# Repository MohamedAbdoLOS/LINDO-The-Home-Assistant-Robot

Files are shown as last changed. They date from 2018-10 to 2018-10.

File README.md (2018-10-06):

# "LINDO" The Home Assistant Robot 
This project introduces a home assistant mobile robot designed to be used for indoor navigation. It can be operated either autonomously or controlled by man remotely over the network. Odometry information is used to estimate the robot's position relative to its origin. In order to achieve a robust odometry, the robot uses two sources of odometry, the linear velocities from the encoders and the angular velocity from the IMU. A Kinect mounted on the robot creates a SLAM map with the help of edge detection and computer vision. The robot can navigate autonomously through the predefined map using AMCL. 

An assistant system is integrated on the robot allows it to communicate and socialize with humans, via a Chatbot powered by Artificial Intelligence and Machine Learning, connected to external APIs to bring realtime information. Also the robot can Automate and Secure your home via an IOT system. 

The project uses The Robots Operating System (ROS) which makes its functionality reusable in other projects. Modularity and readable codes are considered in the design and implementation of software nodes. About future work there is a wide field of updates like object detection, On-line Mapping of new Environments and installation of manipulator (i.e. robot arm) for a variet

## Rendered Designs:
#### Inner Frame:
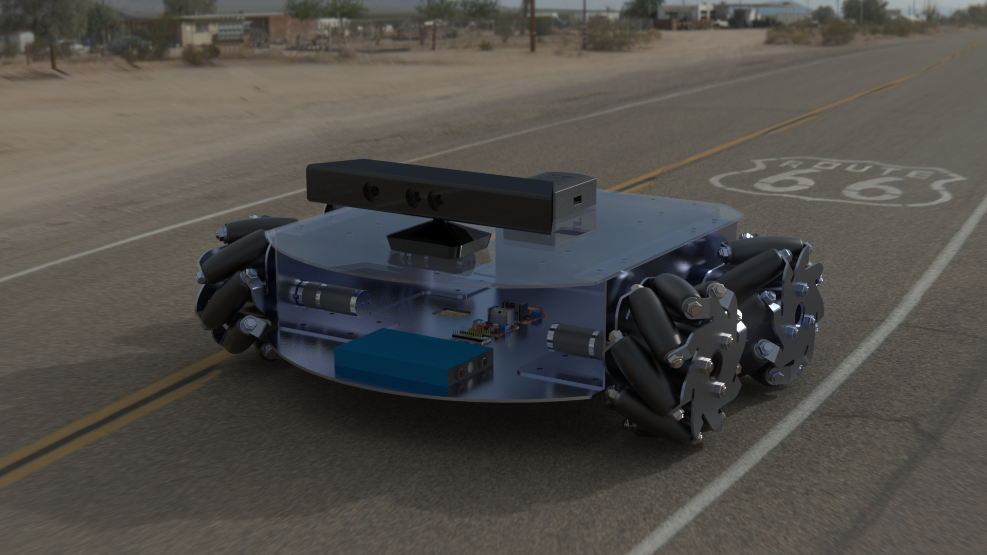
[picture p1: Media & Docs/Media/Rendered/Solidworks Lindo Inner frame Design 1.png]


#### Outer Frame:
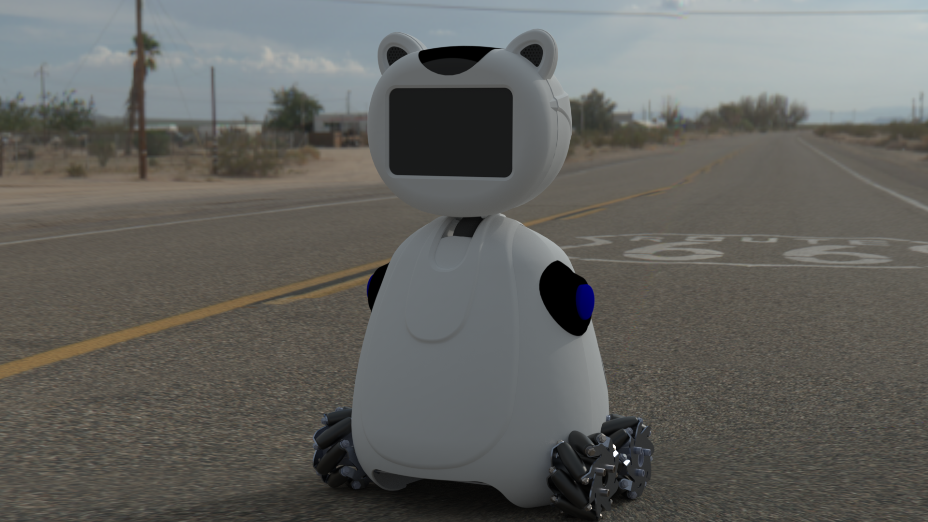
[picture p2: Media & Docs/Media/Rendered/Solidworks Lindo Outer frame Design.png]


## Hardware
- 4 Mecanum Wheels
- 4 Motors 12v 8.8 Kgf.cm
- 4 Encoders 3PPR
- 4 Channels Motor Driver
- Teensy 3.2
- Rasberry PI3
- MPU6050
- Kinect
- 12V Batteries

## Wiring Schematic:
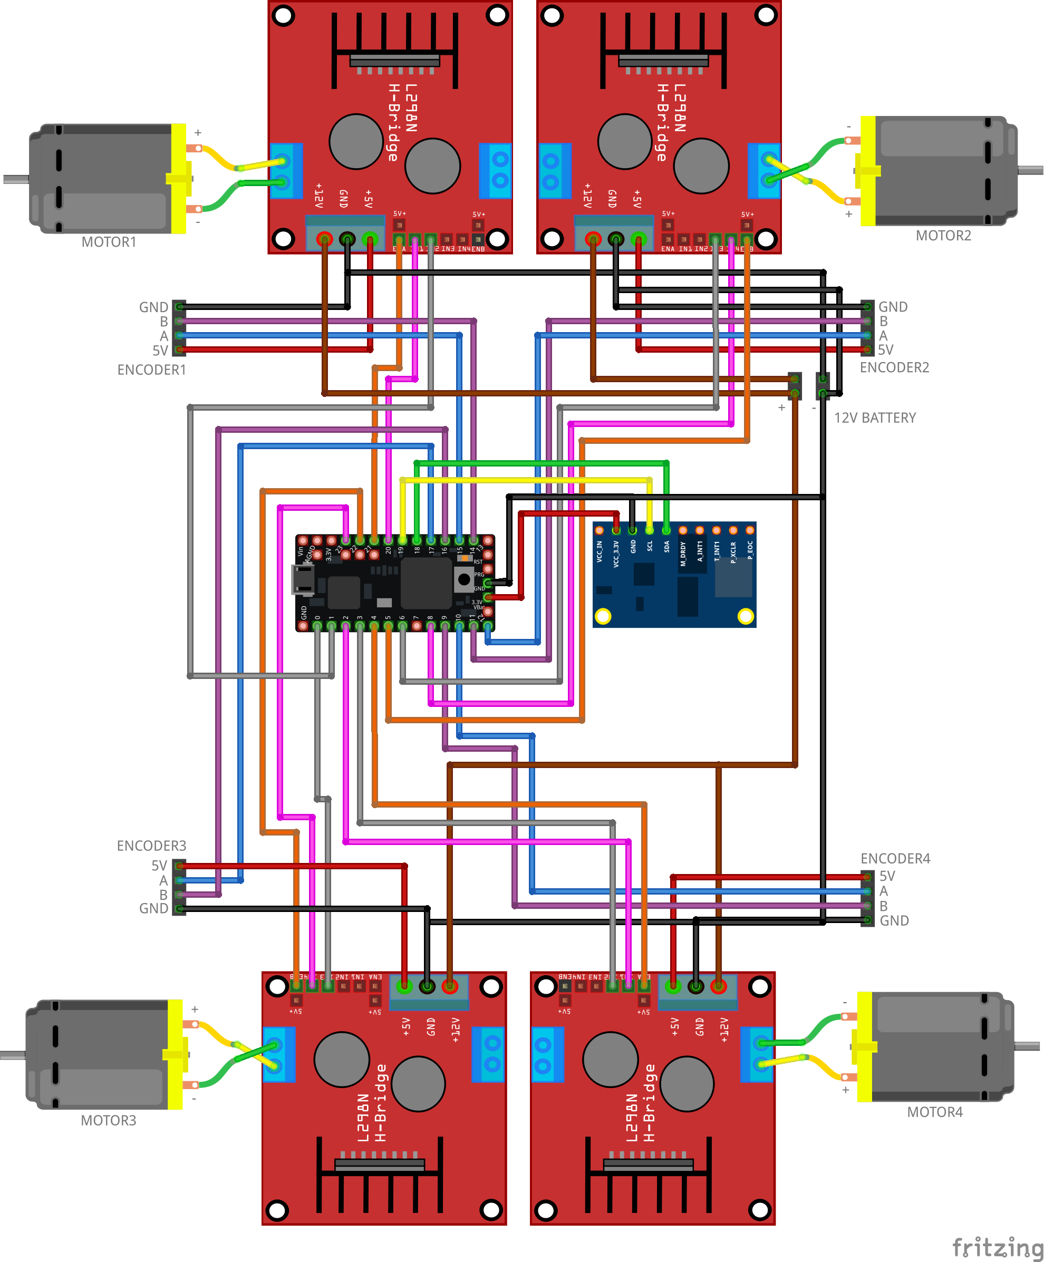
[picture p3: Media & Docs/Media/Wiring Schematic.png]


#### Notes:
- Fritizing doesn't have a 4 Channels Motor Driver yet, so we used an L298 Drivers on the schematic instead.

## Clearifying:
#### Master And Slave:
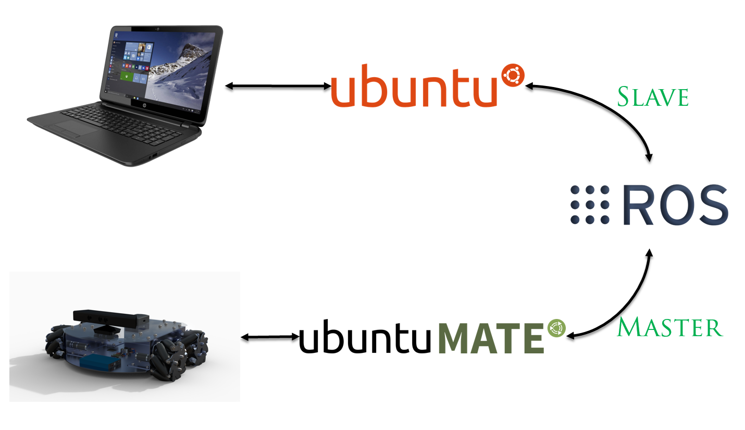
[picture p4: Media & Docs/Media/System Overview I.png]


#### Project Overview:
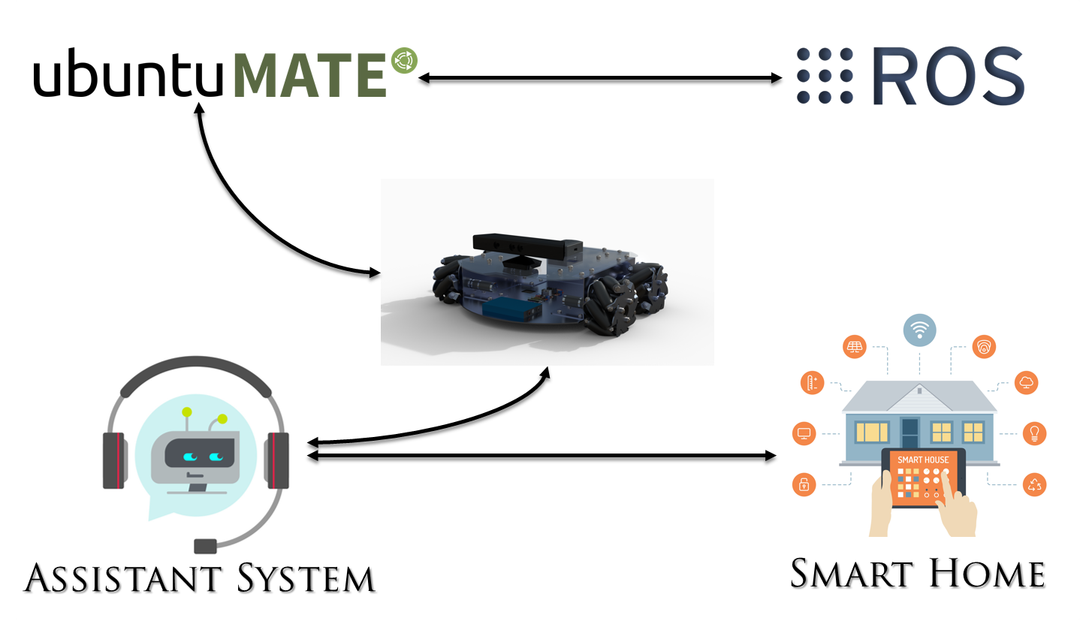
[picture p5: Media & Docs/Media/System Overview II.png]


#### Rasberry PI(ROS) And Teensy:
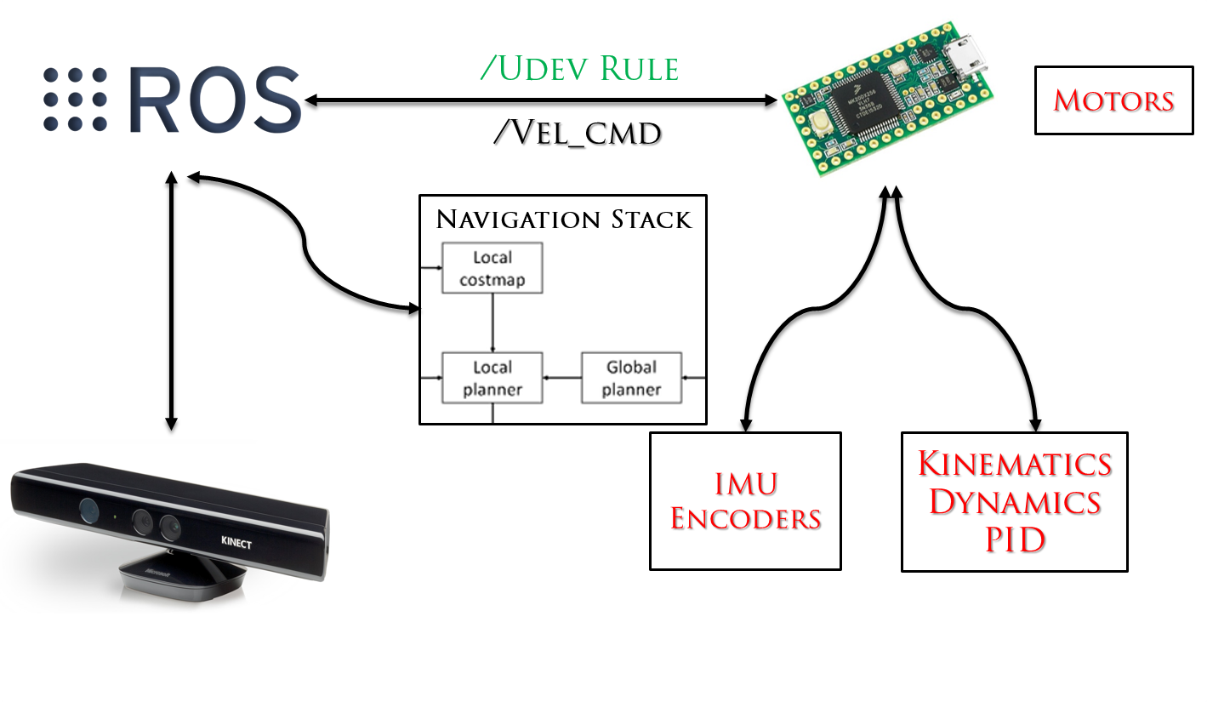
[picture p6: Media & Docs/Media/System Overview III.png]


## Platform:

#### Development Labtop:
- ROS Kinetic (Ubuntu 16.04 Xenial)

#### Rasberry Pi 3:
- ROS Kinetic (Ubuntu Mate 16.04)

## User Manual:
#### Creating a Map:
- On robot’s computer,  Launch base driver:
```
roslaunch lindorobot bringup.launch
```
- On robot’s computer, Launch mapping packages:
```
roslaunch lindorobot slam.launch
```
- On your development computer, run teleop_twist_keyboard:
```
rosrun teleop_twist_keyboard teleop_twist_keyboard.py	
```
- On your development computer, Run rviz:
```
roscd lindo_visualize/rviz
rviz -d slam.rviz
```
- Once you are done mapping save the map by running map_server on the robot's computer:
```
rosrun map_server map_saver -f ~/lindorobot_ws/src/linodorobot/maps/map
```

#### Autonomous Navigation
- Launch base driver, on robot’s computer:
```
roslaunch lindorobot bringup.launch
```
- Launch navigation packages, on robot’s computer:
```
roslaunch lindorobot navigate.launch
```
- On your development computer, run rviz:
```
roscd lindo_visualize/rviz
rviz -d navigate.rviz
```

## Assistant System:
#### Overview Of the Assistant System:
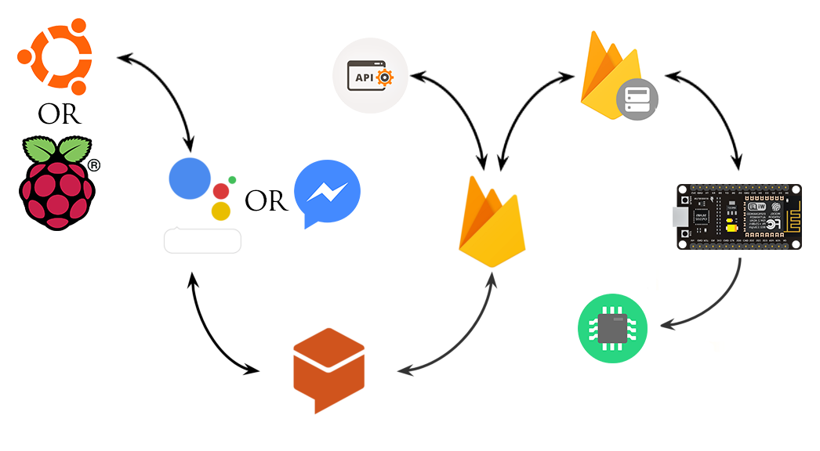
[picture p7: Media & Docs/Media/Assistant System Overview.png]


#### DialogFlow Overview:
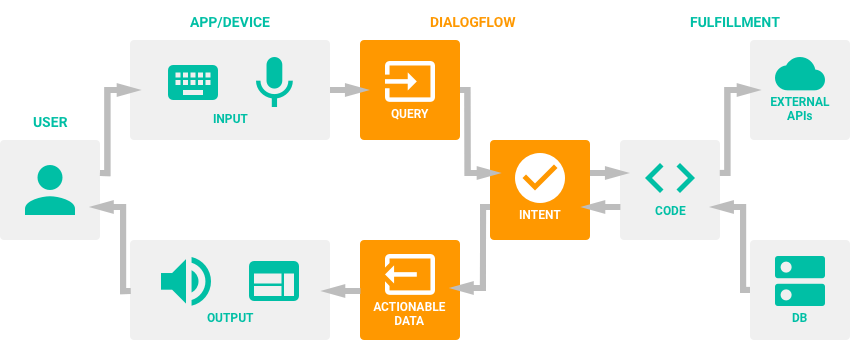
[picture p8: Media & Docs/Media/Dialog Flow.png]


## Videos
- <a href="https://www.youtube.com/watch?v=ZyevQ8gZiK0">"LINDO" - Teleopration Intial Tests[Before PID Tunning]</a>
- <a href="https://www.youtube.com/watch?v=e5AFlajBlEw">"LINDO" - Localization Intial Tests Using IMU and Encoders</a>
- <a href="https://www.youtube.com/watch?v=WcR59p794sQ">"LINDO" - Depth Generation Intial Tests Using Kinect</a>
- <a href="https://www.youtube.com/watch?v=mfHSG0Qb3YM">"LINDO" - Autonomus Driving and Obstacle Avoidance Intial Test </a>
- <a href="https://www.youtube.com/watch?v=wUoYN-ng8Ps">"LINDO" - Assistant System V1 [DialogFlow+Firebase+Database+NodeMCU+APIs]</a>
- <a href="https://www.youtube.com/watch?v=nZiiJRJRGrw">"LINDO" - Assistant System Voice-Ready Intial Test</a>

## TEAM AWAKEN:
#### Members:
- Mohamed Abdo
- Mahmoud Mahmoud
- Islam El-Nagdy
- Ahmed Hamed

#### From:
- MUST University,
- Engineering Faculty,
- Mechatronics Department

#### Contact Us:
- Email: moha_the.best@hotmail.com

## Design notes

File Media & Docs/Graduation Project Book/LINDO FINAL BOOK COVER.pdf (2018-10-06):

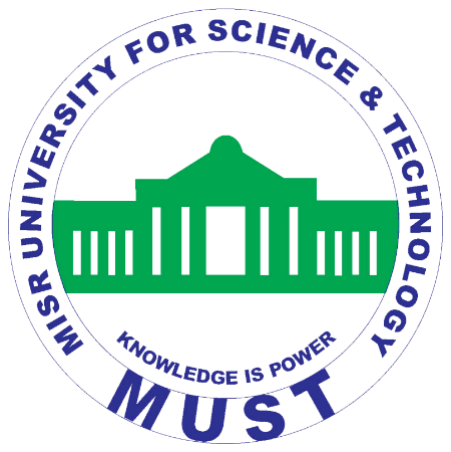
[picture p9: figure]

Misr University for Science & Technology (http://www.must.edu.eg/) Mechatronics Engineering Department Spring/Fall 2017-2018

A B.Sc Senior Project Report Submitted to the Faculty of Engineering at

For the Fulfillment of the Bachelor Degree In

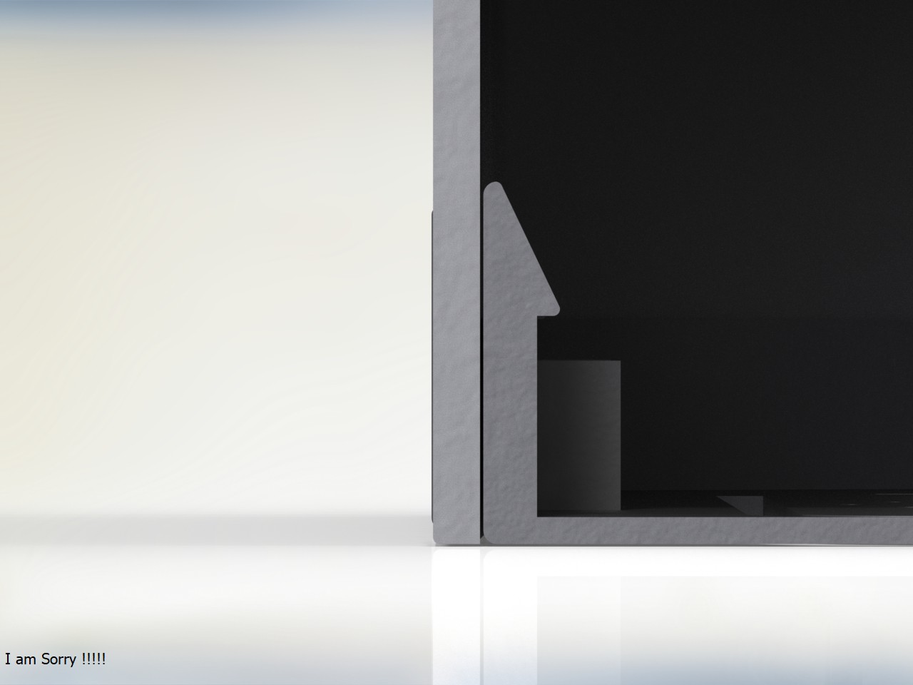
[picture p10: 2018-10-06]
Solidworks Designs/The Robot/Grab Cad folder/Renders/pi section view.JPG

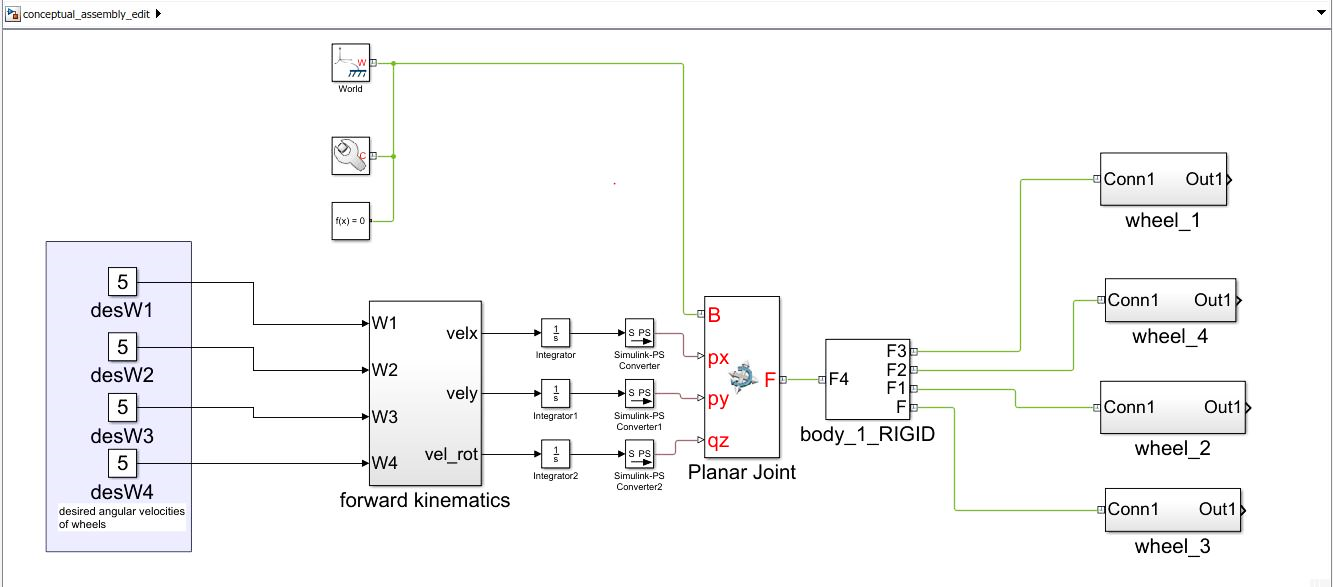
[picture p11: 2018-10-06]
Media & Docs/Media/Kinematics Valdidation I.png

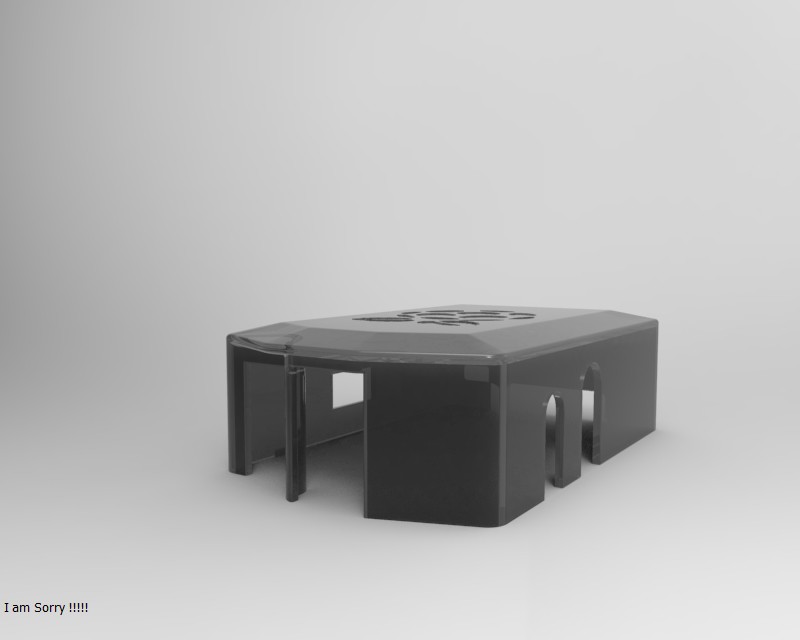
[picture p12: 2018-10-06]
Solidworks Designs/The Robot/Grab Cad folder/Renders/untitled.15.jpg

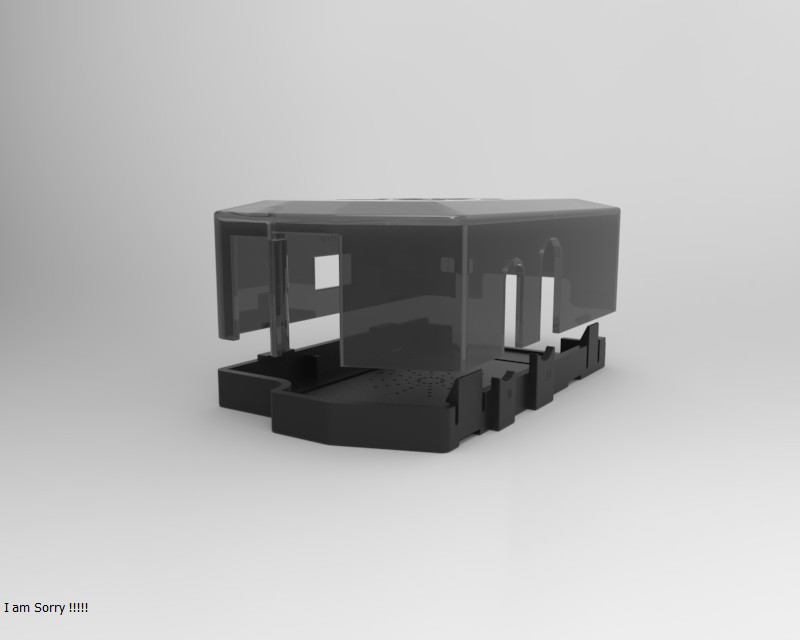
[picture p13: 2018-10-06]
Solidworks Designs/The Robot/Grab Cad folder/Renders/untitled.17.jpg

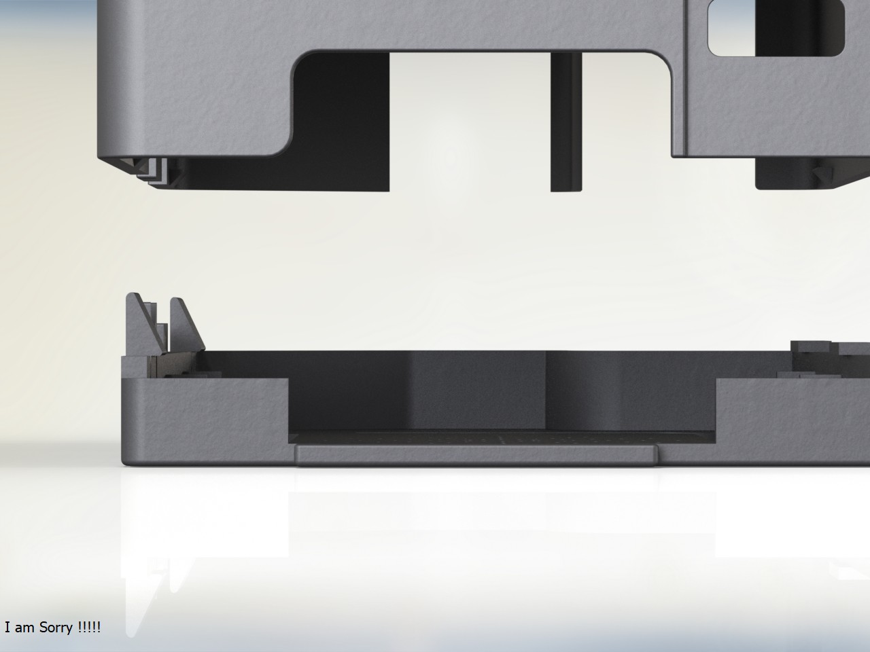
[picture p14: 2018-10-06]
Solidworks Designs/The Robot/Grab Cad folder/Renders/pi8.JPG

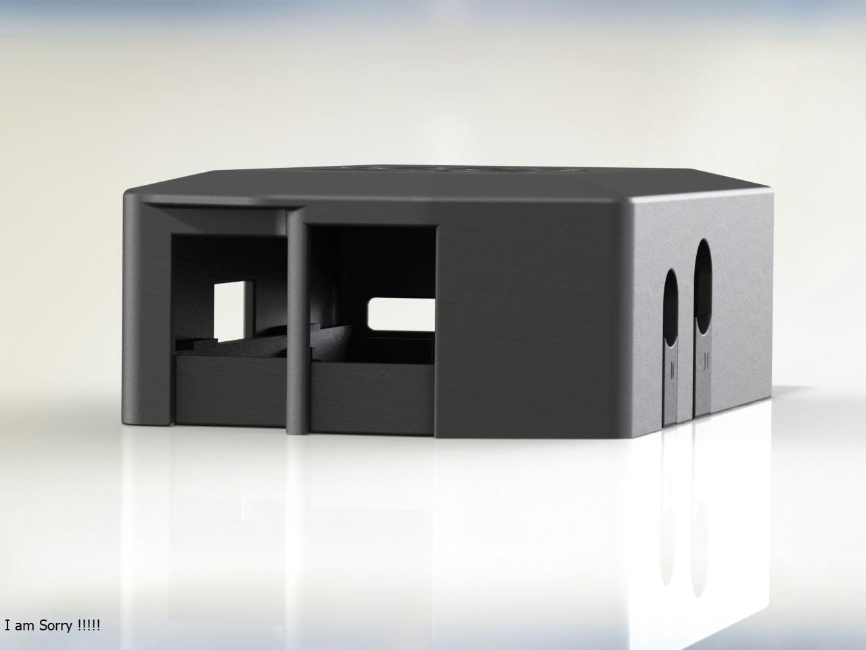
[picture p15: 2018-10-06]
Solidworks Designs/The Robot/Grab Cad folder/Renders/pi14.JPG

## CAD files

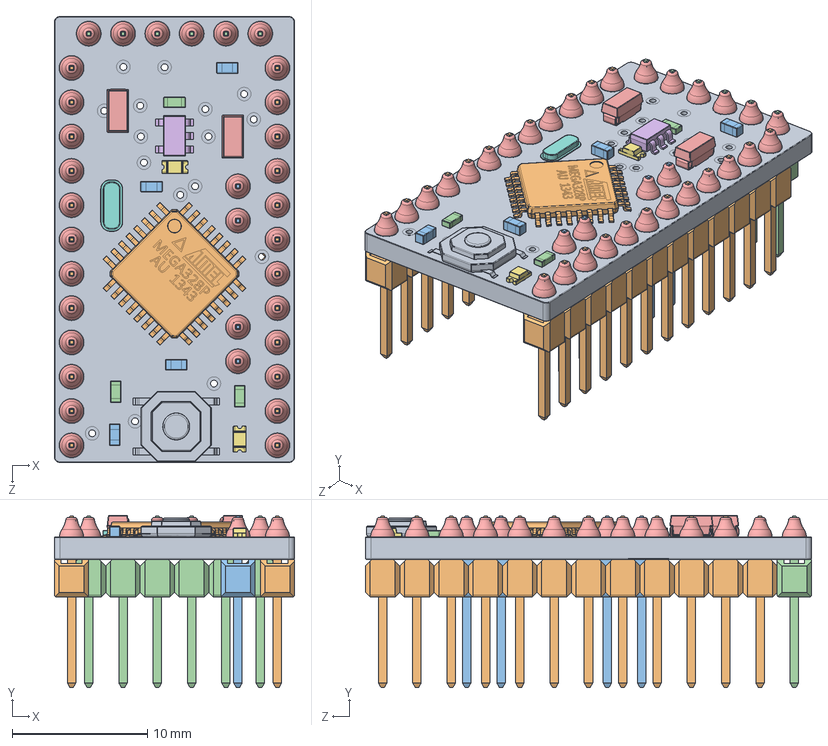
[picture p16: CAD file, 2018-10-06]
Solidworks Designs/The Robot/Arduino Nano/ASSEMBLY.SLDASM
17.8 x 12.7 x 33.0 mm
board
ATmega
cap_603 x 4
res_603 x 3
condensateurTantale_106C x 2
SOT23-5
Surface Mount Chip LED 3.2x1.6mm x 2
TACTILE-SWITCH-SMD-ALT01
Pin Header 1x12 TH Pitch 2.54mm x 2
Pin Header 1x2 TH Pitch 2.54mm x 2
Pin Header 1x6 TH Pitch 2.54mm
solder x 34

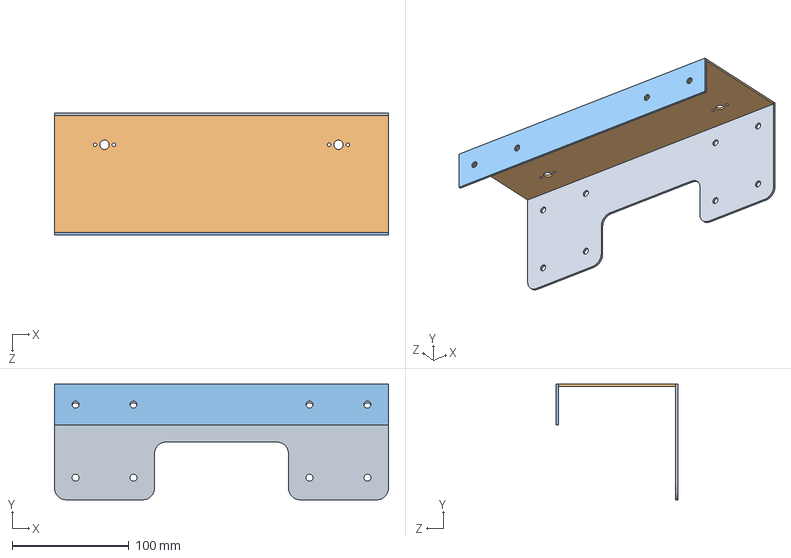
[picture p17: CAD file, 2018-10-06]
Solidworks Designs/The Robot/Base Fixtures/Base Fixture.SLDASM
285.5 x 99.0 x 104.0 mm
BPart1
BPart2
BPart3

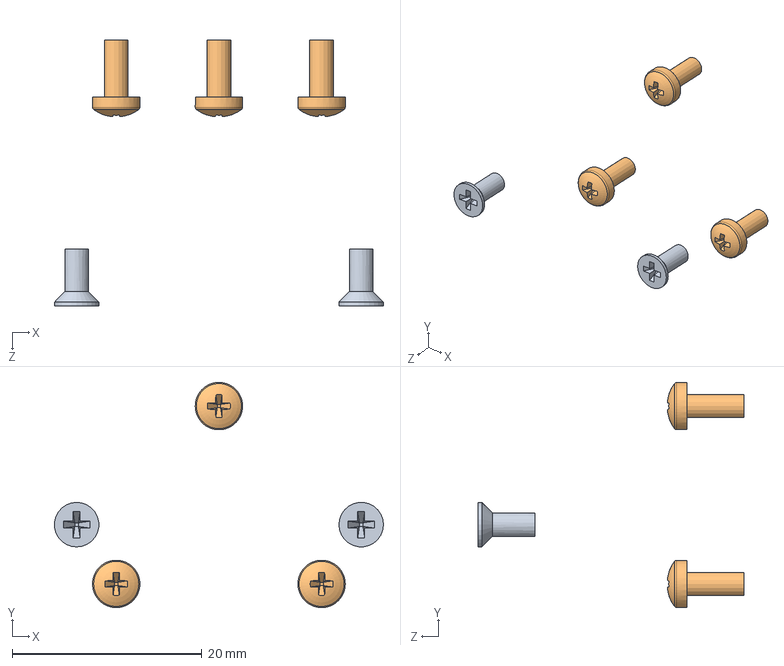
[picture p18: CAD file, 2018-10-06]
Solidworks Designs/The Robot/DC_Motor_Assembly/DC_Motor.SLDASM
34.7 x 23.7 x 28.0 mm
flat head screw_am x 2
pan cross head_am x 3

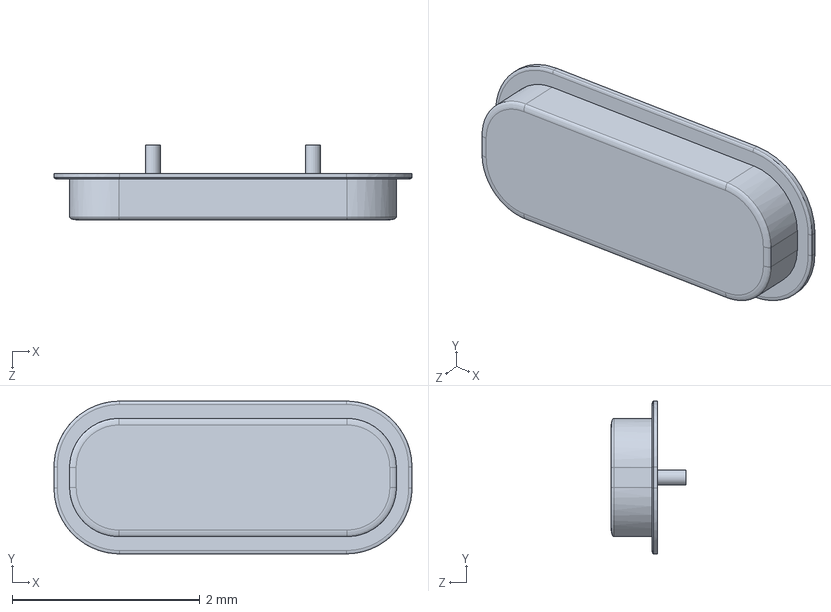
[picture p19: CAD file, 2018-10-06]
Solidworks Designs/The Robot/Arduino Nano/Components/Crystal_Low_Profile.SLDASM
3.82 x 1.63 x 0.795 mm

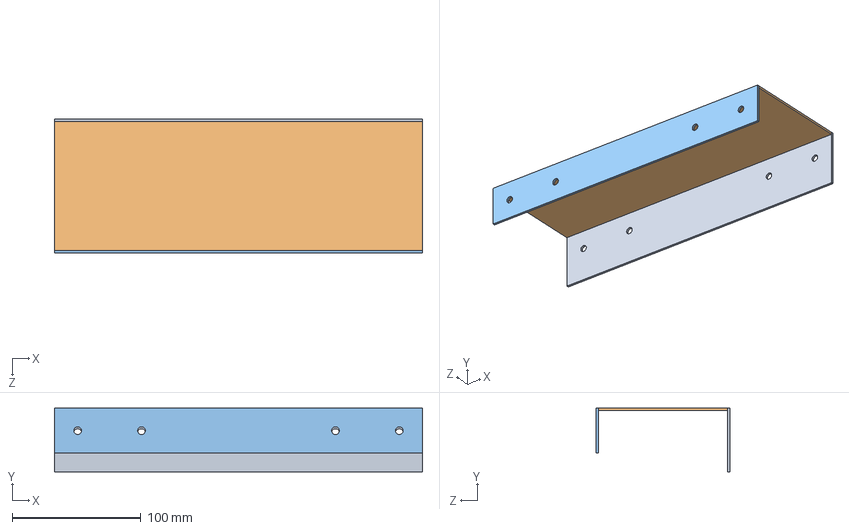
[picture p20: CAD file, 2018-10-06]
Solidworks Designs/The Robot/Base Back Fixture/Base Fixture.SLDASM
285.5 x 49.5 x 104.0 mm
xPart1
xPart2
xPart3

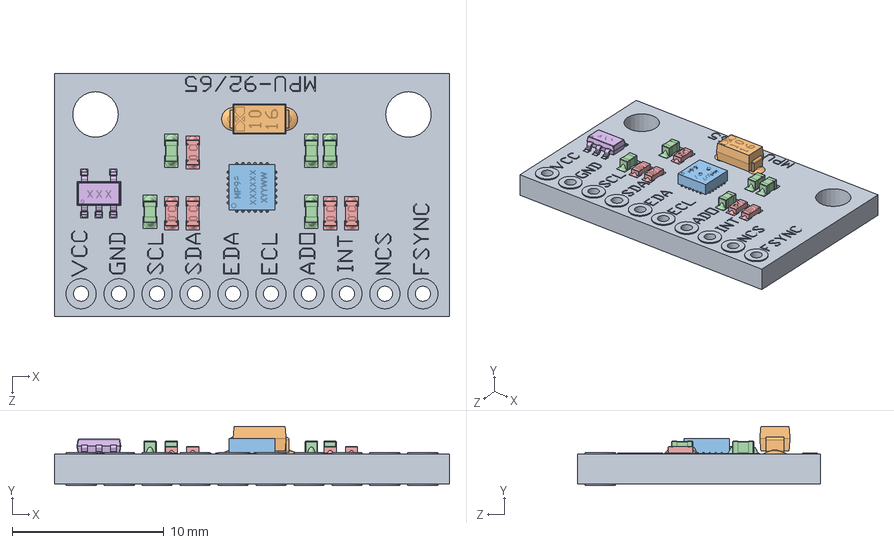
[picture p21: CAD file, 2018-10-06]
Solidworks Designs/The Robot/MPU 92_65/MPU9250.SLDASM
26.0 x 3.91 x 16.0 mm
PCB
C2
MP92
C1 x 5
R1 x 5
V1

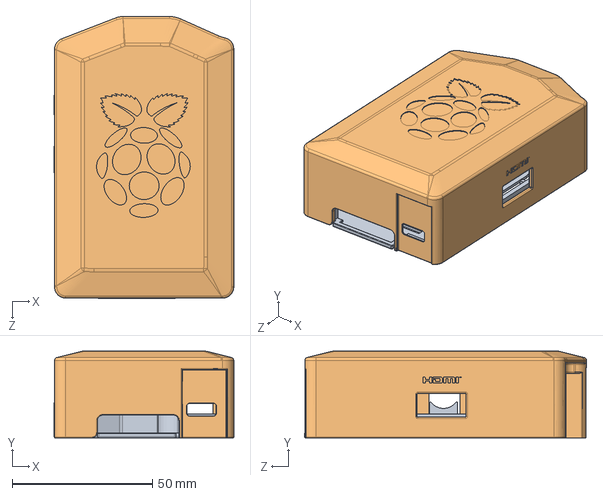
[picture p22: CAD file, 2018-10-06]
Solidworks Designs/The Robot/Grab Cad folder/Assembly.SLDASM
64.1 x 31.0 x 100.7 mm
Botton part
top

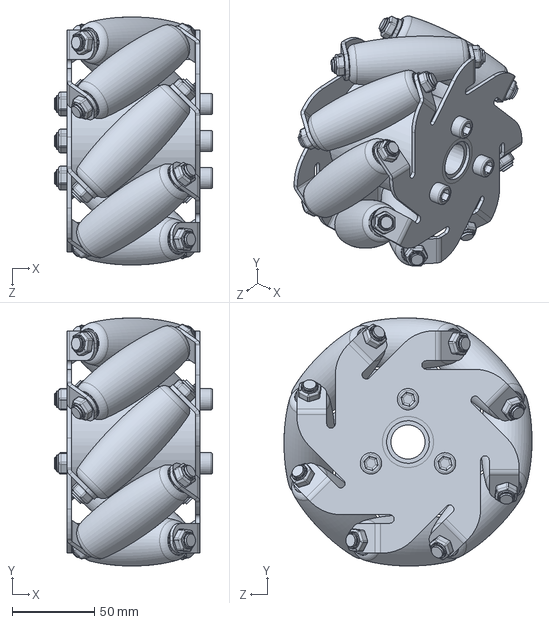
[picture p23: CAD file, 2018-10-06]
Solidworks Designs/The Robot/Mecanum_Wheel_Right_ASM.SLDPRT
96.2 x 150.8 x 150.8 mm

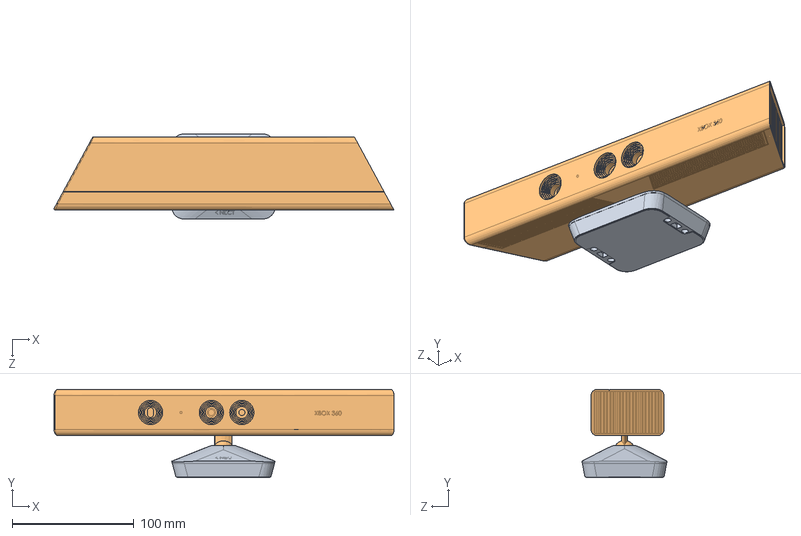
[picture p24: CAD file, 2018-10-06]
Solidworks Designs/The Robot/final kinect.SLDASM
279.3 x 72.5 x 70.0 mm
lower part
kinect upper part

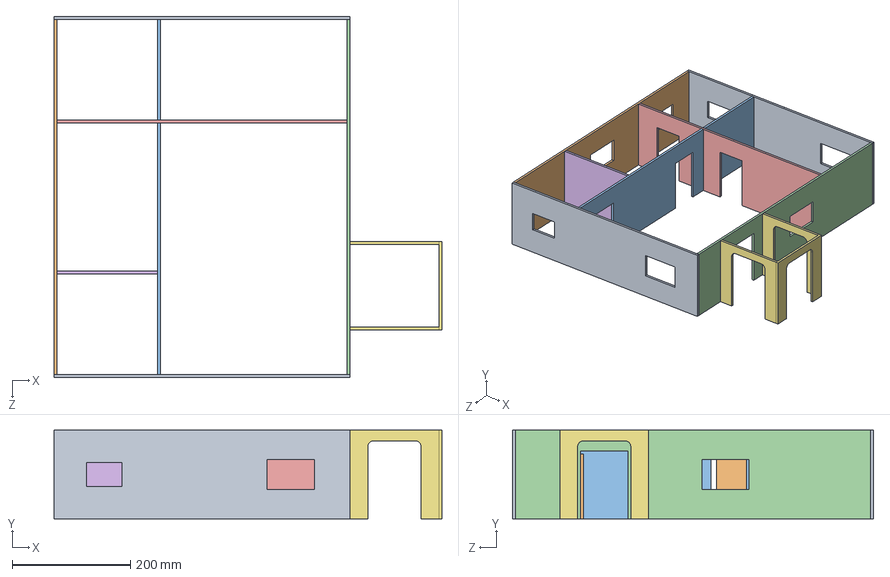
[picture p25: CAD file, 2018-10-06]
Solidworks Designs/Home/Assem1.SLDASM
655.0 x 150.0 x 610.0 mm

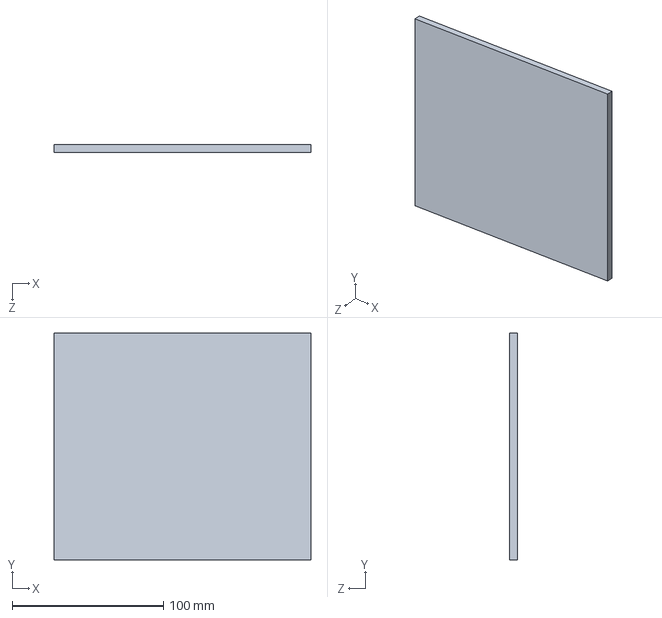
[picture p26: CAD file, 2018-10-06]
Solidworks Designs/Home/Part6.SLDPRT
170.0 x 150.0 x 5.00 mm

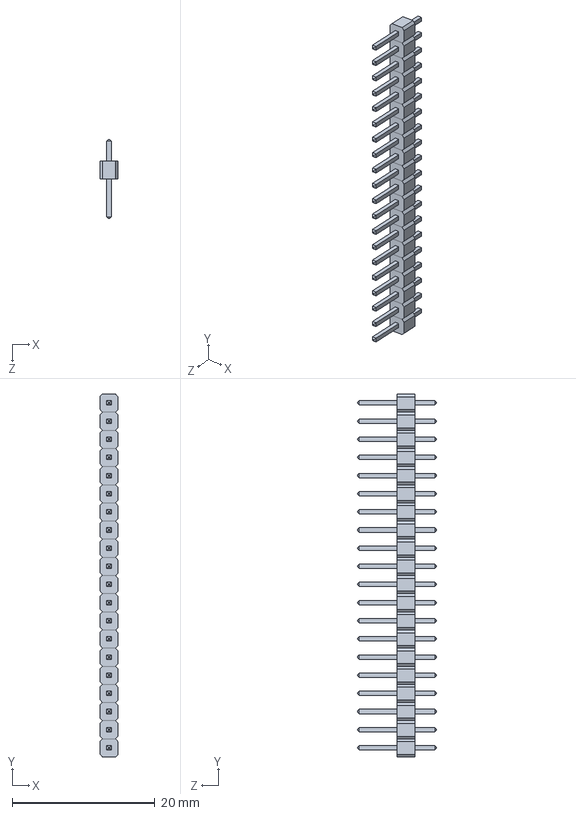
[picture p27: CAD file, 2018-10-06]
Solidworks Designs/The Robot/adafruit-teensy-3-2-header-1.snapshot.2/.100 Header.SLDPRT
2.54 x 50.8 x 11.1 mm

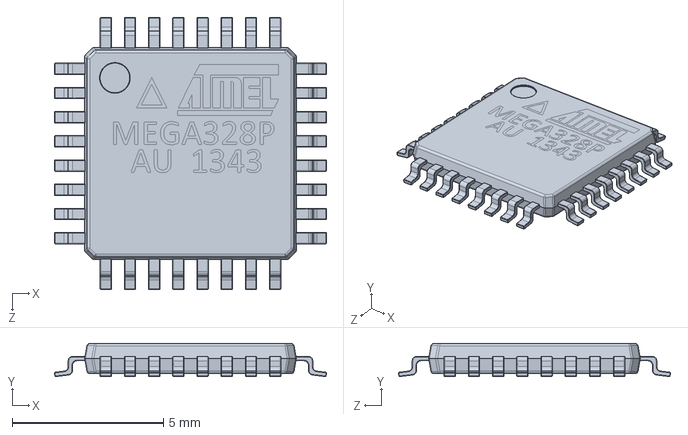
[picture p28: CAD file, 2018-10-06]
Solidworks Designs/The Robot/Arduino Nano/Components/ATmega328 TQFP/ATmega.SLDPRT
9.00 x 1.10 x 9.00 mm

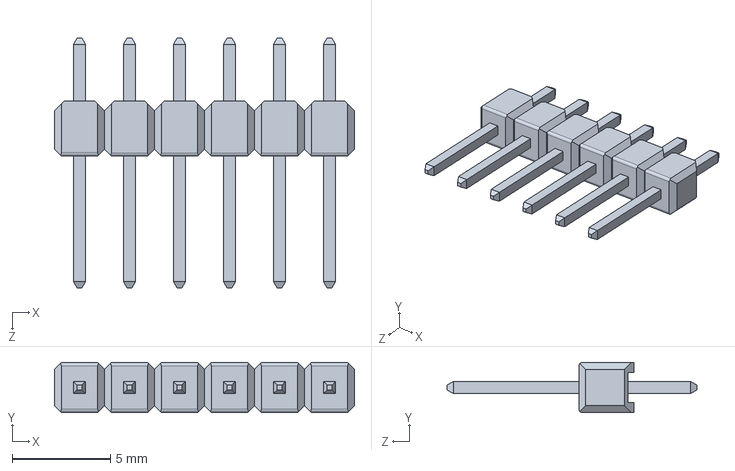
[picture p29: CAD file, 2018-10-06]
Solidworks Designs/The Robot/Arduino Nano/Components/Pin Header 1x6 TH Pitch 2.54mm.SLDPRT
15.2 x 2.54 x 12.7 mm

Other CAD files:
Solidworks Designs/The Robot/Mecanum_Wheel_Left_ASM.SLDPRT
Solidworks Designs/The Robot/Base Back Fixture/xPart2.SLDPRT
Solidworks Designs/The Robot/Base Fixture.SLDPRT
Solidworks Designs/The Robot/Grab Cad folder/Pi finished.SLDPRT
Solidworks Designs/Home/Part1.SLDPRT
Solidworks Designs/Home/Part2.SLDPRT
Solidworks Designs/Home/Part3.SLDPRT
Solidworks Designs/Home/Part4.SLDPRT
Solidworks Designs/Home/Part5.SLDPRT
Solidworks Designs/Home/Part7.SLDPRT
Solidworks Designs/Home/Part8.SLDPRT
Solidworks Designs/The Robot/Arduino Nano/Components/Fusion001.sldprt
Solidworks Designs/The Robot/Arduino Nano/Components/Pin Header 1x12 TH Pitch 2.54mm.SLDPRT
Solidworks Designs/The Robot/Arduino Nano/Components/Pin Header 1x2 TH Pitch 2.54mm.SLDPRT
Solidworks Designs/The Robot/Arduino Nano/Components/SOT23-5.SLDPRT
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

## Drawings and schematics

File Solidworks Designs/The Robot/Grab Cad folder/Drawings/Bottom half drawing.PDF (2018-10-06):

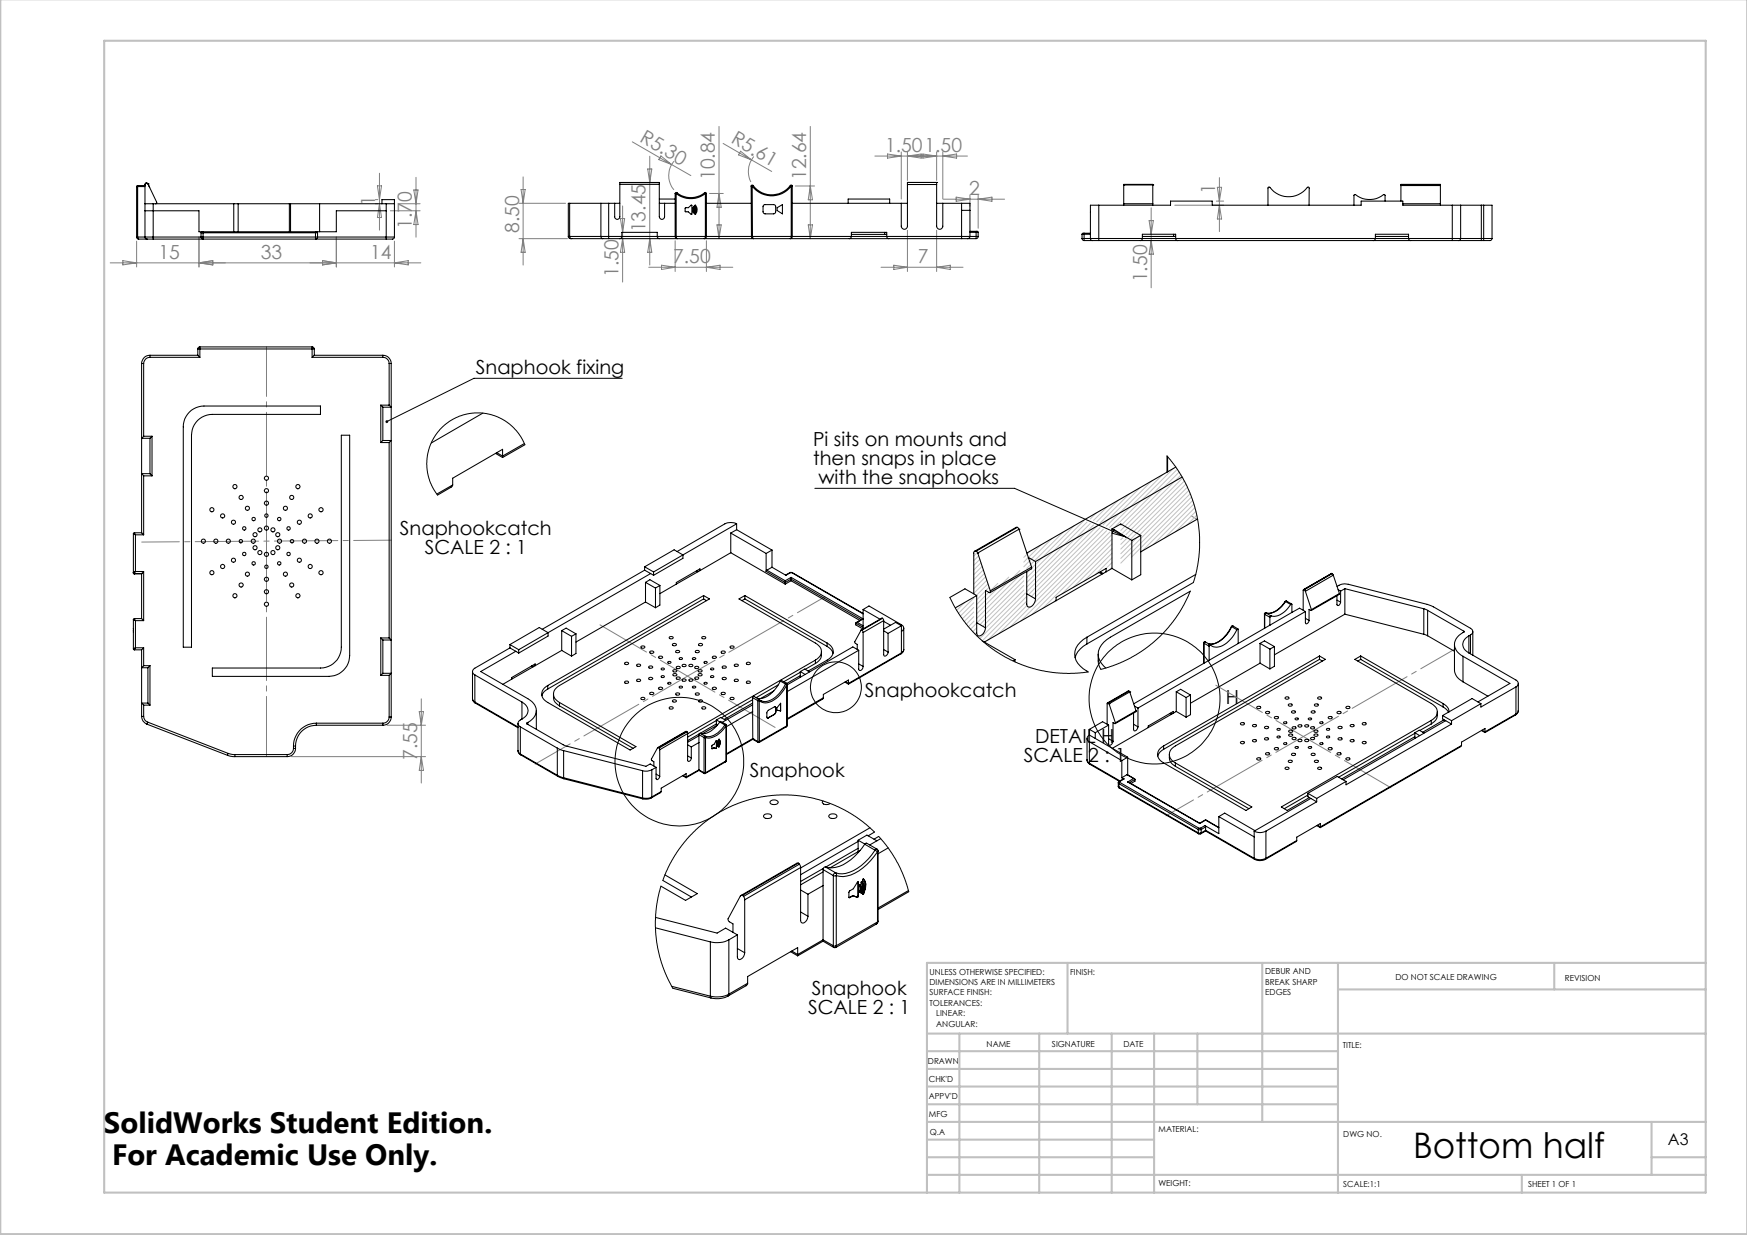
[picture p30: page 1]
Snaphook fixing; SCALE 2 : 1; DETAIL H SCALE 2 : 1; SCALE:1:1; SHEET 1 OF 1; DO NOT SCALE DRAWING; REVISION; DEBUR AND BREAK SHARP; UNLESS OTHERWISE SPECIFIED:; FINISH:

Pi sits on mounts and
then snaps in place
with the snaphooks

DIMENSIONS ARE IN MILLIMETERS
SURFACE FINISH:
TOLERANCES:
LINEAR:
ANGULAR:

NAME | SIGNATURE | DATE | | | | TITLE:
Q.A | | | | MATERIAL: | Bottom half WEIGHT: DWG NO. | A3

DRAWN
CHK'D
APPV'D
MFG

SolidWorks Student Edition.
For Academic Use Only.

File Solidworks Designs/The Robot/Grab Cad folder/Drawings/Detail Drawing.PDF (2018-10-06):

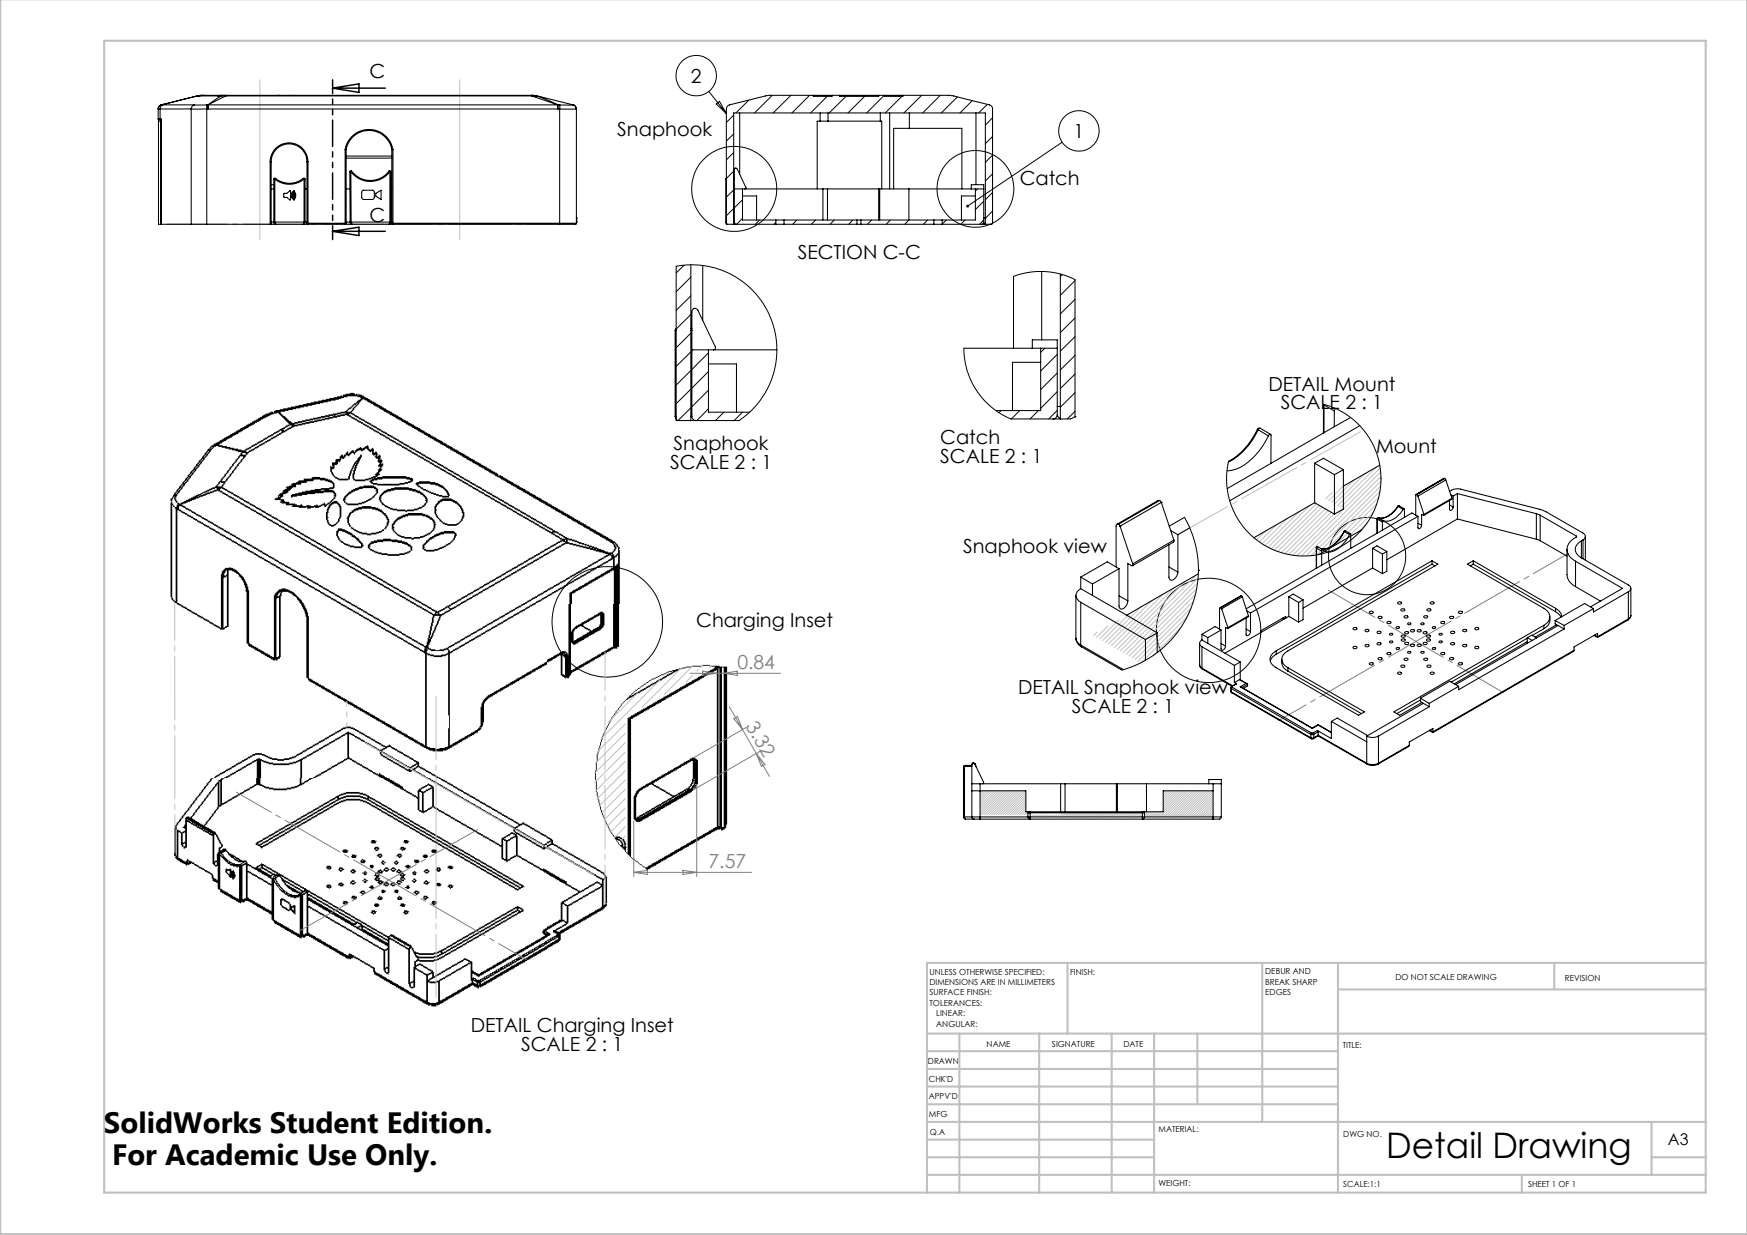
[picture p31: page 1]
SECTION C-C; SCALE 2 : 1; Charging Inset; Snaphook view; DETAIL Mount SCALE 2 : 1; SCALE:1:1; SHEET 1 OF 1; DO NOT SCALE DRAWING; REVISION; DEBUR AND BREAK SHARP; UNLESS OTHERWISE SPECIFIED:; FINISH:

DETAIL Snaphook view
SCALE 2 : 1

DIMENSIONS ARE IN MILLIMETERS
SURFACE FINISH:
TOLERANCES:
LINEAR:
ANGULAR:

DETAIL Charging Inset

NAME | SIGNATURE | DATE | | | | TITLE:
Q.A | | | | MATERIAL: | Detail Drawing WEIGHT: DWG NO. | A3

DRAWN
CHK'D
APPV'D
MFG

SolidWorks Student Edition.
For Academic Use Only.

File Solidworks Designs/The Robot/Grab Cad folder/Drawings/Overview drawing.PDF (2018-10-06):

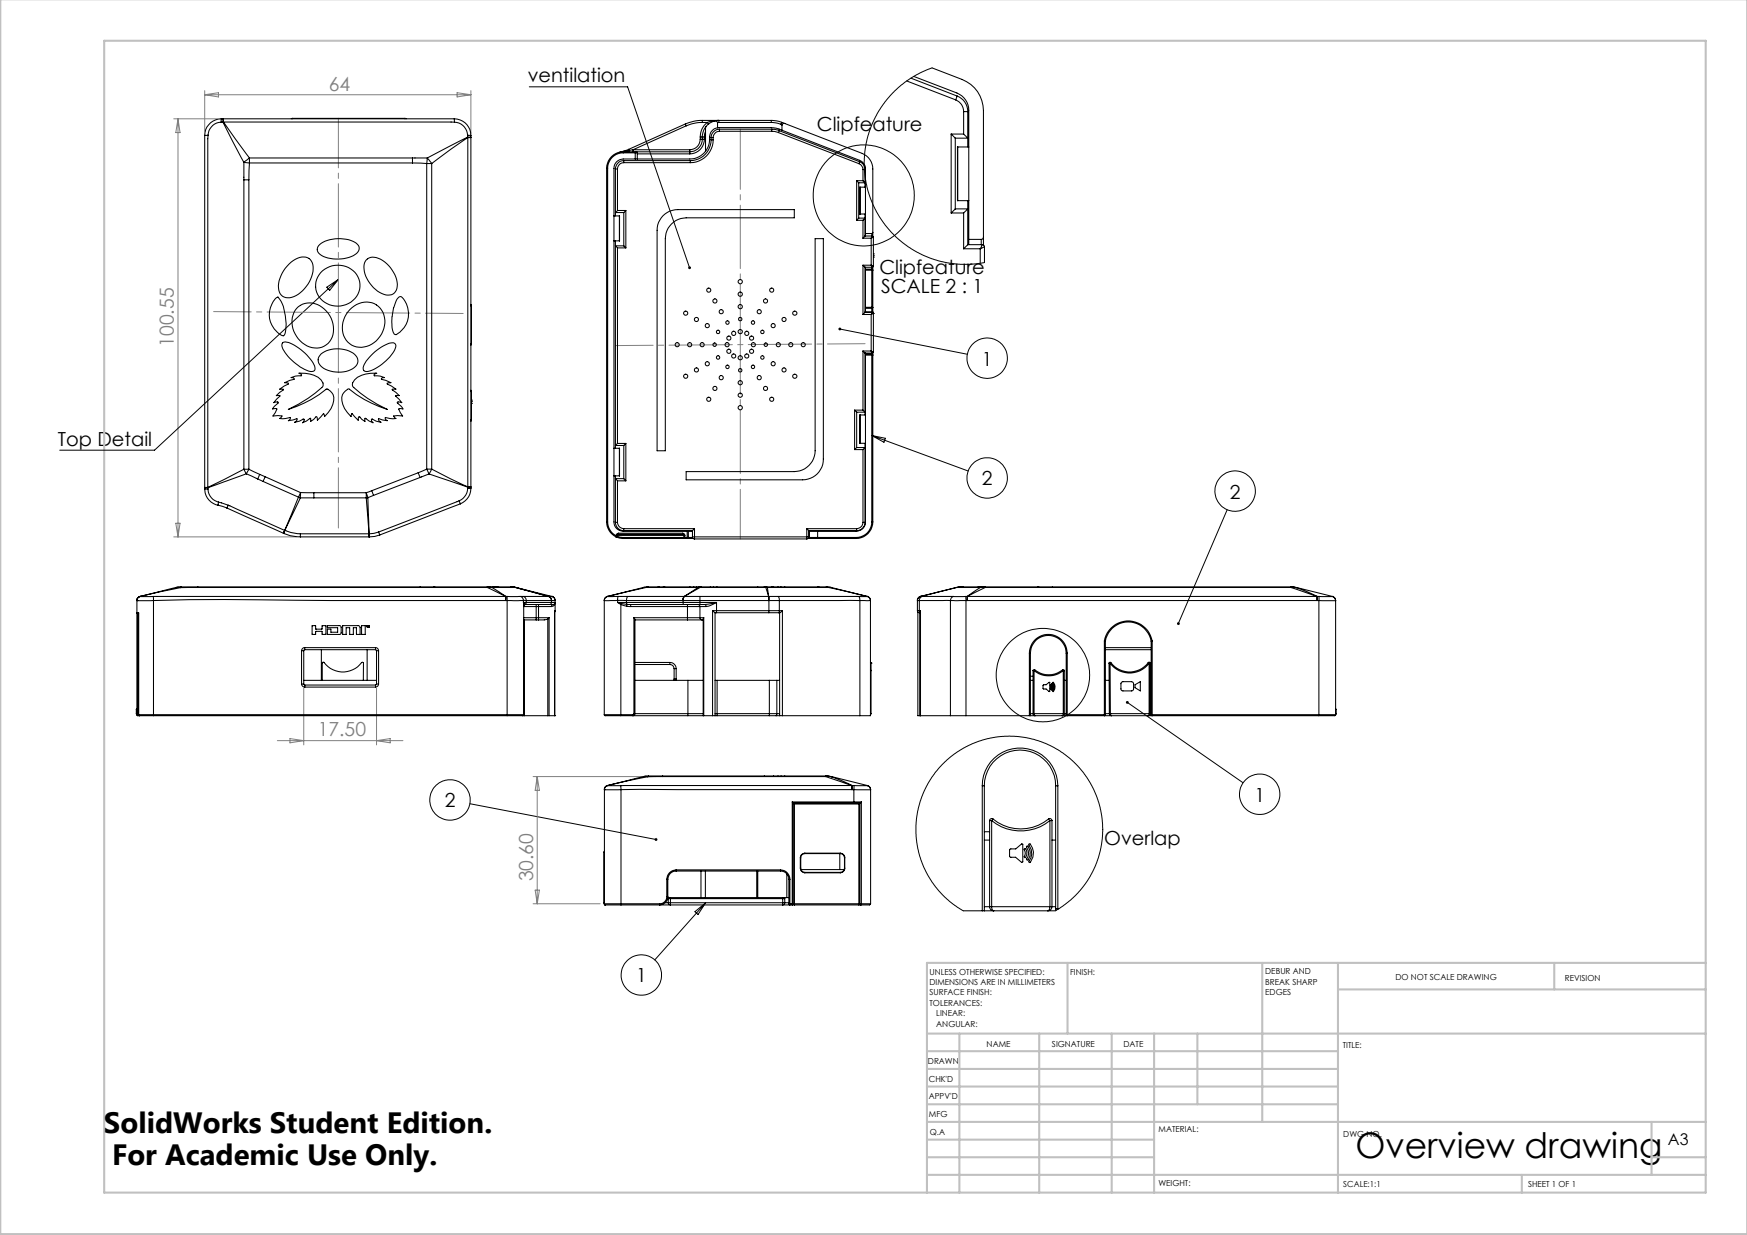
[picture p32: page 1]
Top Detail; SCALE 2 : 1; SCALE:1:1; SHEET 1 OF 1; DO NOT SCALE DRAWING; REVISION; DEBUR AND BREAK SHARP; UNLESS OTHERWISE SPECIFIED:; FINISH:

DIMENSIONS ARE IN MILLIMETERS
SURFACE FINISH:
TOLERANCES:
LINEAR:
ANGULAR:

NAME | SIGNATURE | DATE | | | | TITLE:
Q.A | | | | MATERIAL: | Overview drawing WEIGHT: DWG NO. | A3

DRAWN
CHK'D
APPV'D
MFG

SolidWorks Student Edition.
For Academic Use Only.

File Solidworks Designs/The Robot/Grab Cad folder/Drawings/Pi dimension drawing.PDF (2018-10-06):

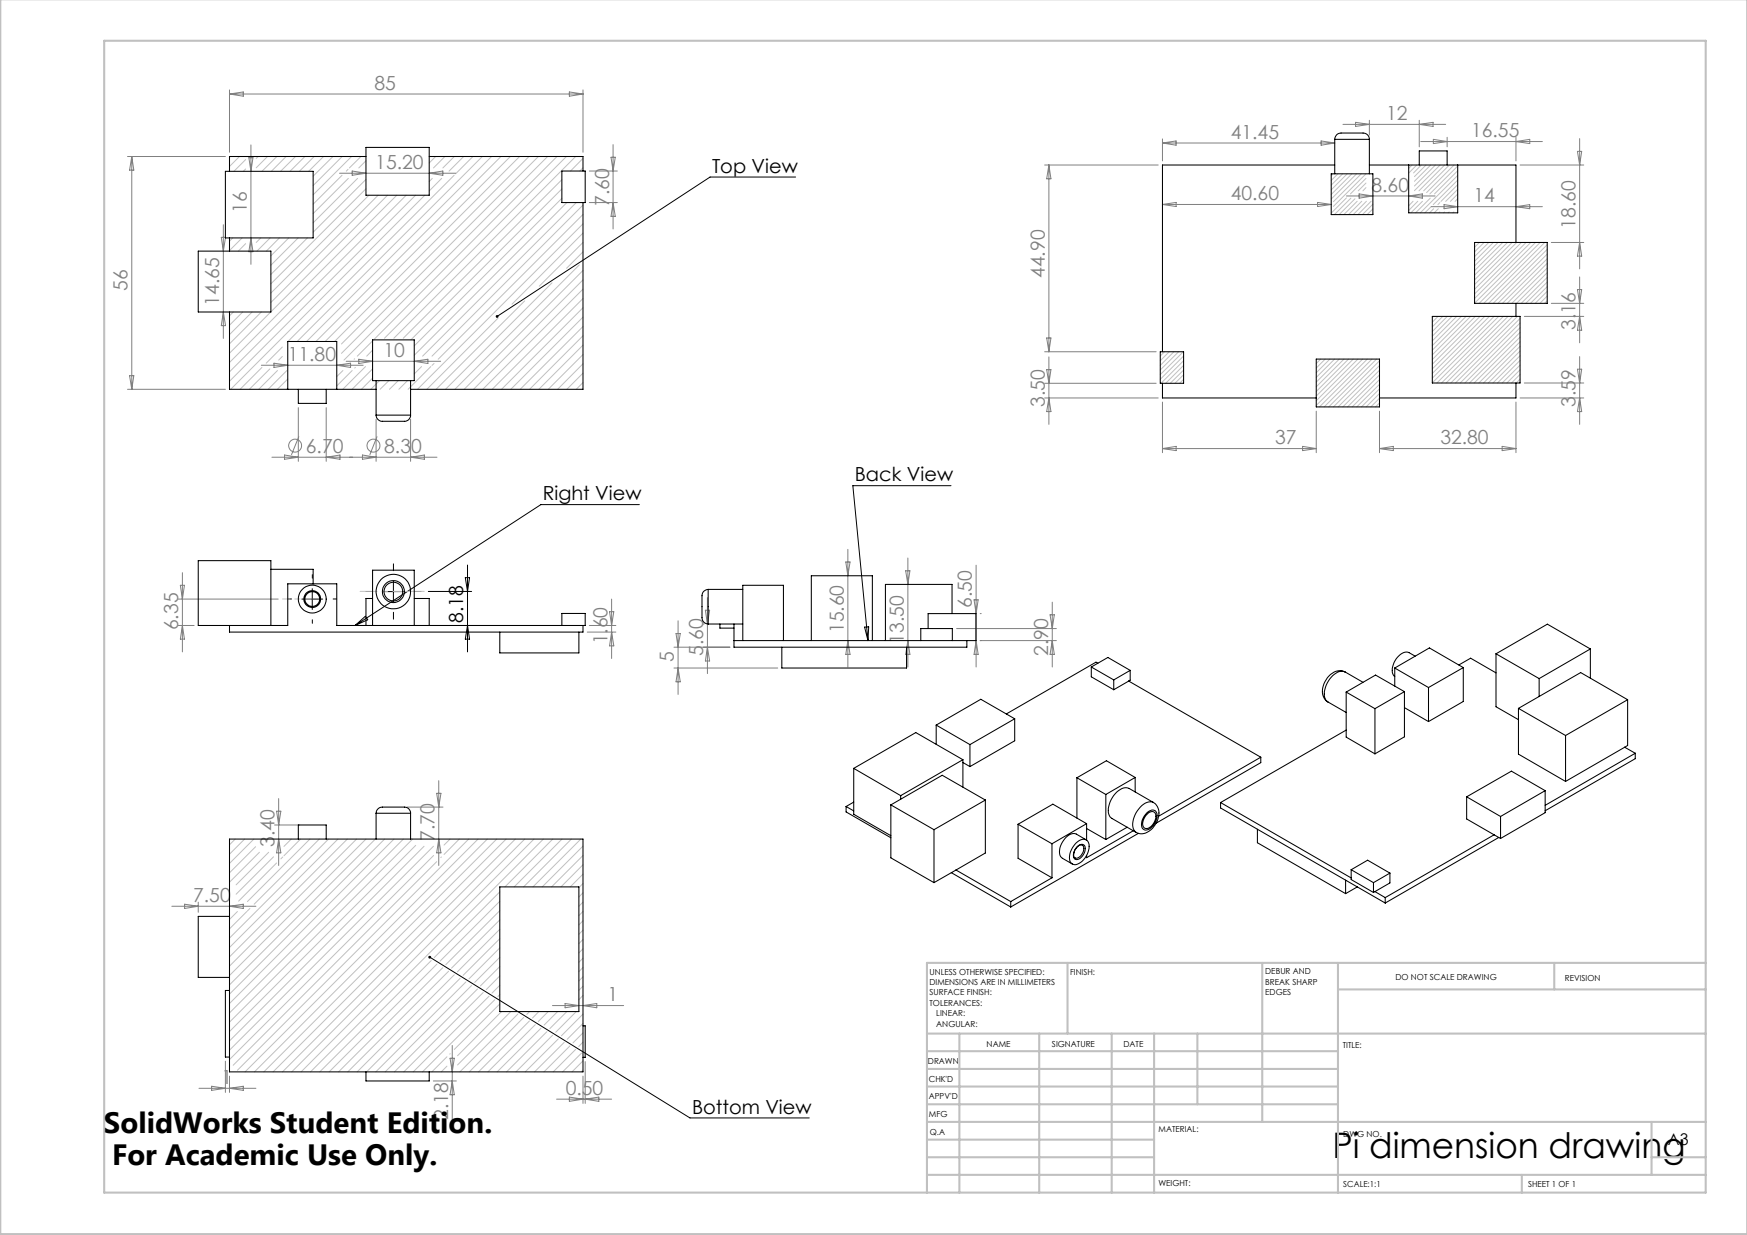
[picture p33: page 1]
Right View; Back View; Bottom View; Top View; SCALE:1:1; SHEET 1 OF 1; DO NOT SCALE DRAWING; REVISION; DEBUR AND BREAK SHARP; UNLESS OTHERWISE SPECIFIED:; FINISH:

DIMENSIONS ARE IN MILLIMETERS
SURFACE FINISH:
TOLERANCES:
LINEAR:
ANGULAR:

NAME | SIGNATURE | DATE | | | | TITLE:
Q.A | | | | MATERIAL: Pi dimension drawing WEIGHT: | DWG NO. | A3

DRAWN
CHK'D
APPV'D
MFG

For Academic Use Only.

SolidWorks Student Edition.

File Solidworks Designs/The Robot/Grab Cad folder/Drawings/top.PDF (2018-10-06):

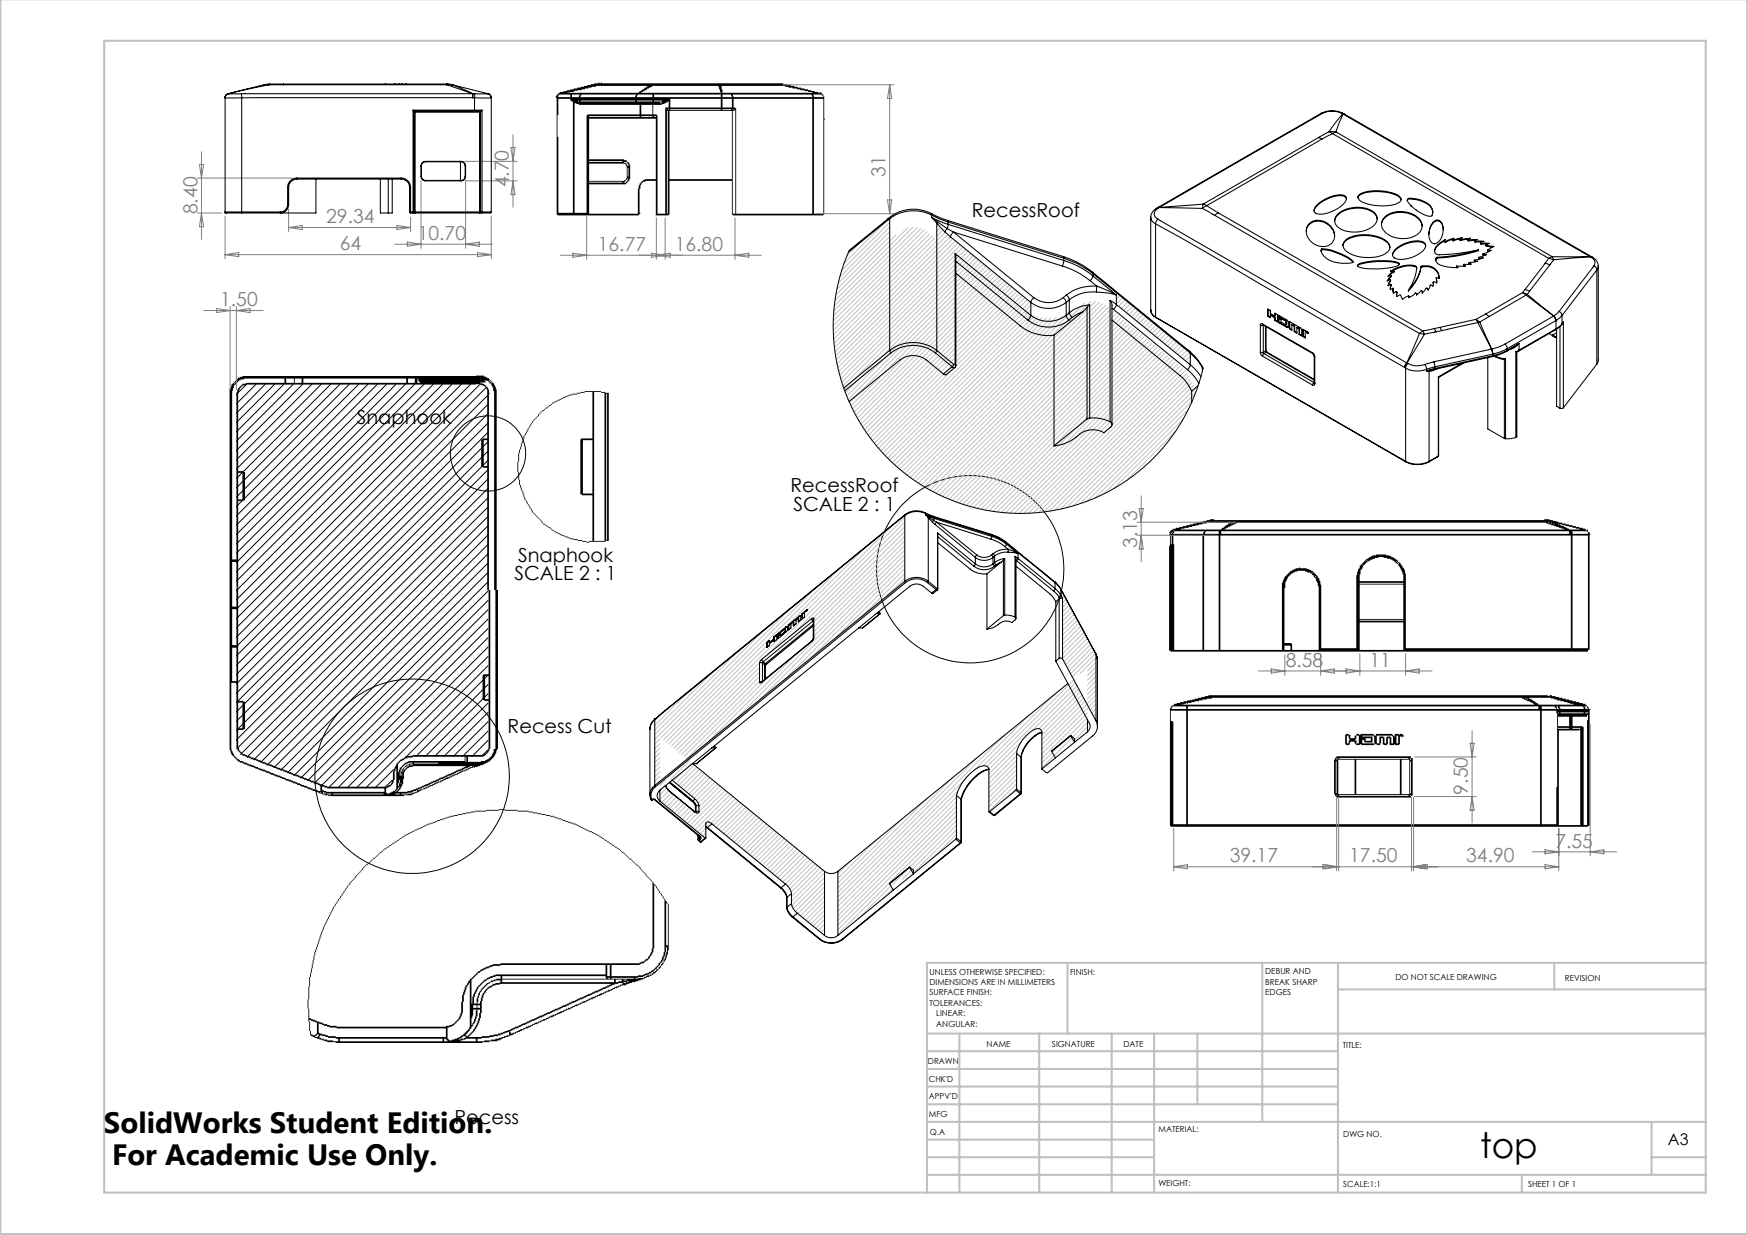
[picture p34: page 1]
Recess Cut; SCALE 2 : 1; SCALE:1:1; SHEET 1 OF 1; DO NOT SCALE DRAWING; REVISION; DEBUR AND BREAK SHARP; UNLESS OTHERWISE SPECIFIED:; FINISH:

DIMENSIONS ARE IN MILLIMETERS
SURFACE FINISH:
TOLERANCES:
LINEAR:
ANGULAR:

NAME | SIGNATURE | DATE | | | | TITLE:

DRAWN
CHK'D
APPV'D
MFG
Q.A | | | | MATERIAL: | top WEIGHT: DWG NO. | A3

SolidWorks Student Edition.
For Academic Use Only.

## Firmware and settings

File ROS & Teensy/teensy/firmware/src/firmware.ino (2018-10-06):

#if (ARDUINO >= 100)
    #include <Arduino.h>
#else
    #include <WProgram.h>
#endif

#include <Servo.h>

#include "ros.h"
#include "ros/time.h"
//header file for publishing velocities for odom
#include "lindo_msgs/Velocities.h"
//header file for cmd_subscribing to "cmd_vel"
#include "geometry_msgs/Twist.h"
//header file for pid server
#include "lindo_msgs/PID.h"
//header file for imu
#include "lindo_msgs/Imu.h"

#include "lindo_base_config.h"
#include "Motor.h"
#include "Kinematics.h"
#include "PID.h"
#include "Imu.h"

#define ENCODER_OPTIMIZE_INTERRUPTS
#include "Encoder.h"

#define IMU_PUBLISH_RATE 10 //hz
#define VEL_PUBLISH_RATE 10 //hz
#define COMMAND_RATE 15 //hz
#define DEBUG_RATE 5

Encoder motor1_encoder(MOTOR1_ENCODER_A, MOTOR1_ENCODER_B);
Encoder motor2_encoder(MOTOR2_ENCODER_A, MOTOR2_ENCODER_B); 
Encoder motor3_encoder(MOTOR3_ENCODER_A, MOTOR3_ENCODER_B); 
Encoder motor4_encoder(MOTOR4_ENCODER_A, MOTOR4_ENCODER_B); 

Motor motor1(Motor::MOTOR_DRIVER, COUNTS_PER_REV, MOTOR1_PWM, MOTOR1_IN_A, MOTOR1_IN_B);
Motor motor2(Motor::MOTOR_DRIVER, COUNTS_PER_REV, MOTOR2_PWM, MOTOR2_IN_A, MOTOR2_IN_B); 
Motor motor3(Motor::MOTOR_DRIVER, COUNTS_PER_REV, MOTOR3_PWM, MOTOR3_IN_A, MOTOR3_IN_B);
Motor motor4(Motor::MOTOR_DRIVER, COUNTS_PER_REV, MOTOR4_PWM, MOTOR4_IN_A, MOTOR4_IN_B);

PID motor1_pid(PWM_MIN, PWM_MAX, K_P, K_I, K_D);
PID motor2_pid(PWM_MIN, PWM_MAX, K_P, K_I, K_D);
PID motor3_pid(PWM_MIN, PWM_MAX, K_P, K_I, K_D);
PID motor4_pid(PWM_MIN, PWM_MAX, K_P, K_I, K_D);

Kinematics kinematics(Kinematics::LINDO_BASE, MAX_RPM, WHEEL_DIAMETER, FR_WHEELS_DISTANCE, LR_WHEELS_DISTANCE, PWM_BITS);

float g_req_linear_vel_x = 0;
float g_req_linear_vel_y = 0;
float g_req_angular_vel_z = 0;

unsigned long g_prev_command_time = 0;

//callback function prototypes
void commandCallback(const geometry_msgs::Twist& cmd_msg);
void PIDCallback(const lindo_msgs::PID& pid);

ros::NodeHandle nh;

ros::Subscriber<geometry_msgs::Twist> cmd_sub("cmd_vel", commandCallback);
ros::Subscriber<lindo_msgs::PID> pid_sub("pid", PIDCallback);

lindo_msgs::Imu raw_imu_msg;
ros::Publisher raw_imu_pub("raw_imu", &raw_imu_msg);

lindo_msgs::Velocities raw_vel_msg;
ros::Publisher raw_vel_pub("raw_vel", &raw_vel_msg);

void setup()
{
    
    
    nh.initNode();
    nh.getHardware()->setBaud(57600);
    nh.subscribe(pid_sub);
    nh.subscribe(cmd_sub);
    nh.advertise(raw_vel_pub);
    nh.advertise(raw_imu_pub);

    while (!nh.connected())
    {
        nh.spinOnce();
    }
    nh.loginfo("LINDOBASE CONNECTED");
    delay(1);
}

void loop()
{
    static unsigned long prev_control_time = 0;
    static unsigned long publish_vel_time = 0;
    static unsigned long prev_imu_time = 0;
    static unsigned long prev_debug_time = 0;
    static bool imu_is_initialized;

    //this block drives the robot based on defined rate
    if ((millis() - prev_control_time) >= (1000 / COMMAND_RATE))
    {
        moveBase();
        prev_control_time = millis();
    }

    //this block stops the motor when no command is received
    if ((millis() - g_prev_command_time) >= 400)
    {
        stopBase();
    }

    //this block publishes velocity based on defined rate
    if ((millis() - publish_vel_time) >= (1000 / VEL_PUBLISH_RATE))
    {
        publishVelocities();
        publish_vel_time = millis();
    }

    //this block publishes the IMU data based on defined rate
    if ((millis() - prev_imu_time) >= (1000 / IMU_PUBLISH_RATE))
    {
        //sanity check if the IMU is connected
        if (!imu_is_initialized)
        {
            imu_is_initialized = initIMU();

            if(imu_is_initialized)
                nh.loginfo("IMU Initialized");
            else
                nh.logfatal("IMU failed to initialize. Check your IMU connection.");
        }
        else
        {
            publishIMU();
        }
        prev_imu_time = millis();
    }

    //this block displays the encoder readings. change DEBUG to 0 if you don't want to display
    if(DEBUG)
    {
        if ((millis() - prev_debug_time) >= (1000 / DEBUG_RATE))
        {
            printDebug();
            prev_debug_time = millis();
        }
    }
    //call all the callbacks waiting to be called
    nh.spinOnce();
}

void PIDCallback(const lindo_msgs::PID& pid)
{
    //callback function every time PID constants are received from lindo_pid for tuning
    //this callback receives pid object where P,I, and D constants are stored
    motor1_pid.updateConstants(pid.p, pid.i, pid.d);
    motor2_pid.updateConstants(pid.p, pid.i, pid.d);
    motor3_pid.updateConstants(pid.p, pid.i, pid.d);
    motor4_pid.updateConstants(pid.p, pid.i, pid.d);
}

void commandCallback(const geometry_msgs::Twist& cmd_msg)
{
    //callback function every time linear and angular speed is received from 'cmd_vel' topic
    //this callback function receives cmd_msg object where linear and angular speed are stored
    g_req_linear_vel_x = cmd_msg.linear.x;
    g_req_linear_vel_y = cmd_msg.linear.y;
    g_req_angular_vel_z = cmd_msg.angular.z;

    g_prev_command_time = millis();
}

void moveBase()
{
    Kinematics::rpm req_rpm;

    //get the required rpm for each motor based on required velocities, and base used
    req_rpm = kinematics.getRPM(g_req_linear_vel_x, g_req_linear_vel_y, g_req_angular_vel_z);

    //the required rpm is capped at -/+ MAX_RPM to prevent the PID from having too much error
    //the PWM value sent to the motor driver is the calculated PID based on required RPM vs measured RPM
    motor1.spin(motor1_pid.compute(req_rpm.motor1, motor1.getRPM()));
    motor2.spin(motor2_pid.compute(req_rpm.motor2, motor2.getRPM()));
    motor3.spin(motor3_pid.compute(req_rpm.motor3, motor3.getRPM()));  
    motor4.spin(motor4_pid.compute(req_rpm.motor4, motor4.getRPM()));    
}

void stopBase()
{
    g_req_linear_vel_x = 0;
    g_req_linear_vel_y = 0;
    g_req_angular_vel_z = 0;
}

void publishVelocities()
{
    Kinematics::velocities vel;

    motor1.updateSpeed(motor1_encoder.read());
    motor2.updateSpeed(motor2_encoder.read());
    motor3.updateSpeed(motor3_encoder.read());
    motor4.updateSpeed(motor4_encoder.read());
    
    //calculate the robot's speed based on rpm reading from each motor and platform used.
    vel = kinematics.getVelocities(motor1.getRPM(), motor2.getRPM(), motor3.getRPM(), motor4.getRPM());

    //pass velocities to publisher object
    raw_vel_msg.linear_x = vel.linear_x;
    raw_vel_msg.linear_y = vel.linear_y;
    raw_vel_msg.angular_z = vel.angular_z;

    //publish raw_vel_msg object to ROS
    raw_vel_pub.publish(&raw_vel_msg);
}

void publishIMU()
{
    //pass accelerometer data to imu object
    raw_imu_msg.linear_acceleration = readAccelerometer();

    //pass gyroscope data to imu object
    raw_imu_msg.angular_velocity = readGyroscope();

    //pass accelerometer data to imu object
    raw_imu_msg.magnetic_field = readMagnetometer();

    //publish raw_imu_msg object to ROS
    raw_imu_pub.publish(&raw_imu_msg);
}


float mapFloat(long x, long in_min, long in_max, long out_min, long out_max)
{
    return (float)(x - in_min) * (out_max - out_min) / (float)(in_max - in_min) + out_min;
}

void printDebug()
{
    char buffer[50];

    sprintf (buffer, "Encoder FrontLeft  : %ld", motor1_encoder.read());
    nh.loginfo(buffer);
    sprintf (buffer, "Encoder FrontRight : %ld", motor2_encoder.read());
    nh.loginfo(buffer);
    sprintf (buffer, "Encoder RearLeft   : %ld", motor3_encoder.read());
    nh.loginfo(buffer);
    sprintf (buffer, "Encoder RearRight  : %ld", motor4_encoder.read());
    nh.loginfo(buffer);
}
